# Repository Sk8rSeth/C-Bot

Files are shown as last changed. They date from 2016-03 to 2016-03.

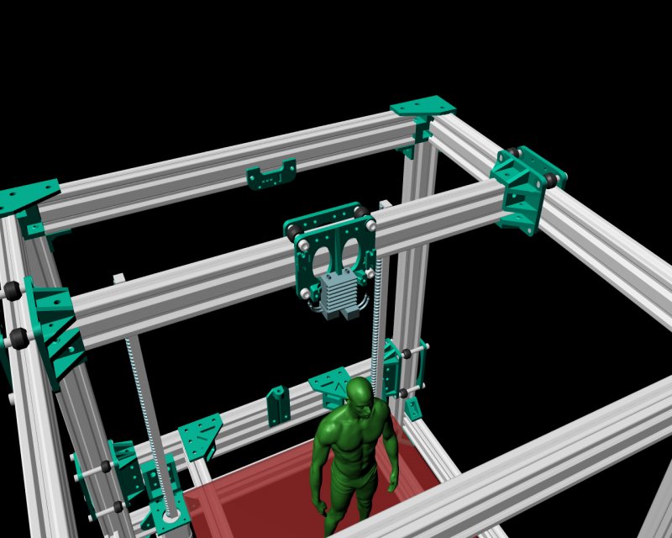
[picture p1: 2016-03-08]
Completed_Builds/Carl_Feniak_Original_C-Bot/Documentation/Assembly Guide/coreXY_detail.jpg

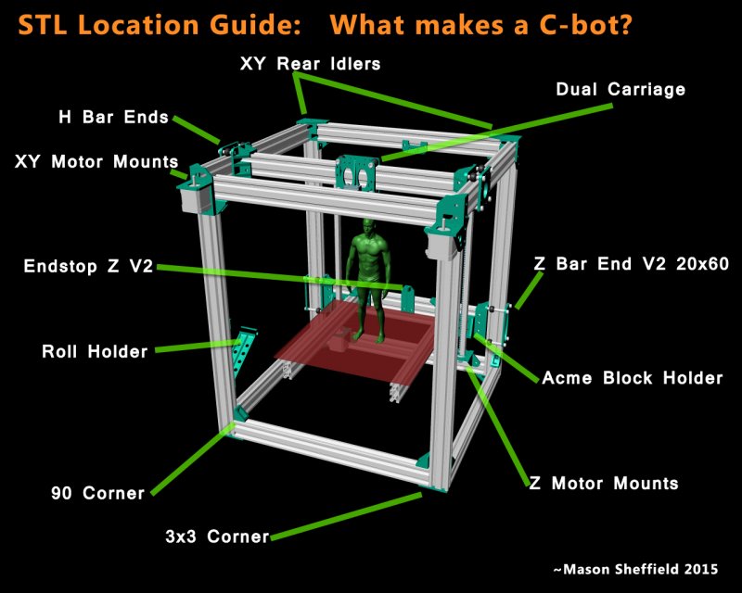
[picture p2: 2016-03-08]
Completed_Builds/Carl_Feniak_Original_C-Bot/Documentation/Assembly Guide/cbot_stlGuide.jpg

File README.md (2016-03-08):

# C-Bot

This repo will serve as the file hosting/iterating source for Carl's C-Bot and its various incarnations.
To contribute to this build, YOUR build must be based on Carl's original c-bot design.
It must be CoreXY mechanics, and most importantly, opensource.

### Anyone is welcome to fork, pull or otherwise grab these files

this will also serve as a place to test experimental builds and parts

# Your Own Build:

file names will be as follows:
	
	- {original_filename}{(#_times_to_print)}.{Author}.{version}
	ex:
		- X_EndStop(x1).CarlFeniak.V2.stl
		- V-Wheel_Spacer(x16).CarlFeniak.v1.stl

### Folder structure MIGHT be as follows, SUBJECT TO CHANGE

{Your Name - Your Build}/

	- Parts/
		- Main_Frame/
		- Z-Bed/
		- XY_Gantry/
		- Other/
		- Test_Parts [each to be deleted when incorporated into final build]/

	- Other_Files [BOM, etc]/

	- Instructions [if any]/

	README.md

the readme.md is the place to show all sorts of info on your build, link to your build log somewhere or thingiverse. its what is displayed when looking at your folder on github.
just like this file is displayed. it might also be a good idea to include YOUR folder structure if its different than the standard, and/or any other notes or progress reports or whatever needs to be seen when looking at your build.

### if you want to add your build to the list, simply submit a pull request with the proper folder structure

Master branch will always be 'stable'. so new people can pull down the master branch at any time and have stable finished builds, that are orginized and easy to navigate. 

### Please create your build in a new branch, named the same as your build to keep pull requests easy

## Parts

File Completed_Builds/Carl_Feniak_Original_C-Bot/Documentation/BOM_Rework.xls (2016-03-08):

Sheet: C-Bot BOM
Price Information Accurate Feb. 2016
BOM
Hardware | AMOUNT | Default | COUNT | USD | Alternatives | COUNT | USD | COMMENT
20x40 Extrusion, 1m | 9 | OpenBuilds, Silver (http://openbuildspartstore.com/v-slot-linear-rail/) | 9 | $18.14 | OpenBuilds, Black (http://openbuildspartstore.com/v-slot-linear-rail/) | 9 | $19.96 | Exact amount depends on the heated bed dimension you get
V-Slot Mini V Wheel | 4x5 | OpenBuilds, Derlin (http://openbuildspartstore.com/delrin-mini-v-wheel/) | 20 | $1.25 | OpenBuilds, Extreme (http://openbuildspartstore.com/xtreme-mini-v-wheel/) | 20 | $3.58
V-Wheel Bearings | 40 | Ebay, MR105ZZ (http://www.ebay.com/itm/10pcs-MR105-MR105ZZ-Miniature-Bearings-Ball-Mini-Bearing-5-X-10-X-4mm-/390391020251) | 4 | $3.28 | Ebay, MR105-2RS (http://www.ebay.ca/itm/10pcs-MR105-2RS-Rubber-Sealed-Ball-Bearing-Miniature-Bearing-5-x-10-x-4mm-Blue-/331662658625) | 4 | $4.00 | you can get the rubber seals in cool colors
Precision shim | 20 | OpenBuilds (http://openbuildspartstore.com/mini-v-wheel-precision-shim/) | 20 | $0.28 |  |  |  | Needed between each pair of V-wheel bearings
Short Spacers | 32 | 3D Print (http://www.openbuilds.com/builds/c-bot.1146/) | 0 | $0.00 | Spacer, 6mm (http://openbuildspartstore.com/aluminum-spacers/) | 40 | $0.28
Long Spacers | 8 | 3D Print (http://www.openbuilds.com/builds/c-bot.1146/) | 0 | $0.00 | Spacer, 20mm (http://openbuildspartstore.com/aluminum-spacers/) | 8 | $0.63
 |  |  |  |  | Extra shims to use above two (http://openbuildspartstore.com/mini-v-wheel-precision-shim/) | 40 | $0.28
8mm lead Screw | 30-50cm x2 | Ebay, combo (http://www.ebay.ca/itm/500mm-Length-Lead-Screw-8mm-Screw-Pitch-Brass-Nut-for-Reprap-3D-Printer-Z-Axis-/261941269628) | 2 | $12.00 | MTW, two start (http://store.makerstoolworks.com/motion/two-start-lead-screw-and-nut-single/) | 2 | $24.95 | 4 Start is typical, but 2 start would be better if you can source it in the length needed
5mm/8mm Flex Coupling | 2 | Ebay, Spiral Type (http://www.ebay.ca/itm/5x8-mm-Motor-Jaw-Shaft-Coupler-5mm-To-8mm-Flexible-Coupling-OD-19x25mm-SU-/221594917783) | 2 | $1.10 | Ebay, Jaw Clamp Type (http://www.ebay.ca/itm/400525695992?_trksid=p2060353.m1438.l2649&ssPageName=STRK%3AMEBIDX%3AIT) | 2 | $8.59 | 3D print (http://www.thingiverse.com/thing:366040)
GT2 16 Tooth Pulley | 2 | Ebay (http://www.ebay.ca/itm/2pcs-GT2-Aluminum-Timing-Pulleys-RepRap-Prusa-Mendel-3D-Printer-16-Tooth-Teeth-/141522888429) | 1 | $5.99 | Amazon, combo (http://www.amazon.com/Anycubic-Timing-Pulleys-Meters-Printer/dp/B0152ZNDLK) | 1 | $14.98
GT2 Belt | 2-5m | Ebay (http://www.ebay.ca/itm/5-Meter-197-6mm-Width-GT2-Timing-Belt-For-3D-printer-Rostock-Mendel-REPRAP-/252232179286) | 1 | $6.20
MK8 drive pulley | 1-2 | Ebay (http://www.ebay.ca/itm/Feedstock-Wheel-Extruder-Gear-Hobbed-Gear-Drive-Gear-for-Reprap-3D-printer-good-/121349742050) | 1 | $2.00 | Ebay, alternate (http://www.ebay.com/itm/1-75-3mm-3D-Printer-MK8-Drive-Gear-for-RepRap-Makerbot-Filament-Extruder-Pulley-/252055736275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)
F623ZZ Flange Bearing | 16 | Ebay (http://www.ebay.com/itm/10-x-F623zz-Mini-Metal-Double-Shielded-Flanged-Ball-Bearings-/231540202636) | 2 | $4.99 | Ebay, alternate (http://www.ebay.ca/itm/10pcs-Mini-F623ZZ-3x10x4mm-Double-Shielded-Flange-Ball-Bearing-Flanged-Bearing-/252169403902) | 2 | $5.60
625ZZ Bearing (for extruder) | 1-2 | Ebay (http://www.ebay.ca/itm/2pcs-625ZZ-Miniature-Bearings-ball-Mini-Bearing-5mm-16mm-5mm-/141204979309) | 1 | $1.99 | Ebay, alternate (http://www.ebay.ca/itm/2pcs-625ZZ-Miniature-Bearings-ball-Mini-Bearing-5mm-16mm-5mm-/141204979309) | 1 | $1.98
1/8" Push In Fitting | 2-4 | Ebay (http://www.ebay.ca/itm/5pcs-1-8-Push-In-Fittings-F-bowden-extruder-1-75mm-4mm-OD-PTFE-Tube-3D-Printer-/331723162262) | 1 | $4.00
Bulldog clips | 8 | Ebay (http://www.ebay.ca/itm/10x-Mini-19mm-Metal-Fold-Back-Letter-Notes-Receipt-Money-File-Paper-Binder-Clips-/351587197720) | 1 | $1.50 | Amazon (http://www.amazon.com/Officemate-Silver-Binder-Assorted-31021/dp/B00006IBA2?s=office-products) | 1 | $2.89
Bed Leveling Springs | 4 | Ebay (http://www.ebay.ca/itm/NEW-4pcs-Heated-Bed-Spring-8mm-3D-Printer-DIY-Accessories-/331324945571) | 1 | $4.00 | homedepot (http://www.homedepot.com/p/Everbilt-Spring-Assortment-Kit-84-Pack-15642/202045461) | 1 | $4.37
Extuder Spring | 1-2 | Hobby Shop? | 1 | $1.00 | Ebay, 7mm OD 25mm L (http://www.ebay.ca/itm/0-6mm-Wire-Diameter-5-50mm-L-304-Stainless-Steel-Pressure-Compression-Spring-/281912361412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) | 1 | 9.99 | Mine was from a random spring kit
Heated Bed, various sizes | 1 | Maker Farm (http://www.makerfarm.com/index.php/heat-beds/12-x-12-heat-bed.html) | 1 | $46.50 | Ebay (http://www.ebay.com/itm/RepRap-PCB-Heatbed-200x300mm-Dual-power-12-24V-Perfect-for-Prusa-i3-etc-/281311483823) | 1 | $19.20
Heated Bed Insulation | 1 | Cardboard | 1 | $0.00 | Amazon (http://www.amazon.com/gp/product/B0018DHBAK?psc=1&redirect=true&ref_=oh_aui_detailpage_o01_s00) | 1 | $10.40
Glass to match heated bed | 1 | Household Store/IKEA | 1 | $10.00 | Voxel Factory (https://www.voxelfactory.com/collections/hardware/products/custom-cut-borosilicate-glass) | 1 | $42.37 | Picture frame sales are a good source of cheap glass, boresilicate is best though
Cable/Zip Tie, 4+ | 4-8 | Ebay (http://www.ebay.ca/itm/New-100pcs-Black-8-3x200mm-Locking-Nylon-Plastic-Cable-Wire-Zip-Ties-Cord-Wrap-/291198607167) | 1 | $2.68 |  |  |  | to hold tube and wires to XY carriage
Electrical
Nema 17 Motor | 5-6 | ATinc, Nema 17 (http://www.automationtechnologiesinc.com/products-page/3d-printer/nema17-stepper-motor-kl17h247-150-4a-for-3d-printer) | 5 | $8.99 | Ebay (http://www.ebay.ca/itm/1pcs-3D-Printers-Reprap-68g-cm2-Lead-1-8-Degree-12V-1-2A-Nema17-Stepper-Motor-/291595158449) | 5 | $18.33 | get 68oz*in or better
12V/30A Power Supply | 1 | Amazon (http://www.amazon.com/gp/product/B00D7CWSCG?psc=1&redirect=true&ref_=oh_aui_detailpage_o03_s00) | 1 | $23.97 | Ebay (http://www.ebay.ca/itm/Hot-12V-30A-AC-DC-PSU-Regulated-Switching-Power-Supply-350W-Brand-New-/262242869774) | 1 | $33.95 | Or repurpose an old PC power supply
Print Control Board | 1 | Ramps 1.4 Kit, Ebay (http://www.ebay.ca/itm/3D-Printer-Kit-RAMPS-1-4-Mega2560-A4988-12864-LCD-Controller-for-Arduino-Reprap-/252181241032) | 1 | $31.99 | Azteeg X3 (http://www.panucatt.com/Azteeg_X3_reprap_3d_printer_controller_p/ax33dp.htm) | 1 | $109.99 | Ramps comes bundled in many types of packages
Stepper Drivers | 5 | DRV8825, Ebay (http://www.ebay.ca/itm/Geeetech-Stepper-driver-Pololu-DRV8825-StepStick-for-RAMPS-Sanguinololu-Teensylu-/331167037633) | 5 | $1.59 |  |  |  | DRV8825 can handle more amps and higher temps than A4998s
Endstop for Y and Z | 2 | Ebay (http://www.ebay.com/itm/3x-Mechanical-End-Stop-Endstop-Switch-Module-V1-2-3D-printer-Reprap-Mendel-Pursa-/271443703227) | 1 | $4.49
Endstop connectors | 2 | Ebay (http://www.ebay.com/itm/20PCS-4-pins-white-Connector-leads-Head-XH2-54-2-54mm-connector-kit-DIP-4p-/330928070002) | 2 | $1.62
Endstop for XY carraige | 1 | Ebay (http://www.ebay.ca/itm/Toggle-Collision-Limit-switch-Travel-Switch-for-Robot-Arduino-Brand-New/351214665011) | 1 | $1.77
HotEnd | 1-2 | Filastuder, E3D Lite (http://www.filastruder.com/products/lite6) | 1 | $39.99 | Filastuder, E3Dv6 (http://www.filastruder.com/products/all-metal-e3d-v6-hotend) | 1 | $79.99
Heated Bed Thermister | 1 | Ebay (http://www.ebay.com/itm/100Kohm-NTC-thermistor-temperture-sensor-for-Reprap-hotbed-PCB-MK2a-heated-bed-/231204000452) | 1 | $0.99
Power Switch/ receptacle | 1 | Ebay (http://www.ebay.ca/itm/Panel-IEC320-C14-Inlet-Power-Socket-On-Off-SPST-Red-Rocker-Switch-AC-250V-10A-/321513901251) | 1 | $3.94 | Amazon (http://www.amazon.com/gp/product/B00511QVVK?psc=1&redirect=true&ref_=od_aui_detailpages00) | 1 | $4.44
Relay | 1 | Ebay, Mech (http://www.ebay.ca/itm/30A-High-Current-Contactor-Switch-12V-Electric-Relay-Board-DC-Power-Control-new-/221977262205) | 1 | $4.26 | Amazon, SSR (http://www.amazon.com/Single-Phase-SSR-40DD-DC3-32V-DC5-60V/dp/B012SW6TB6?s=hi) | 1 | $11.71
Cooling Fan, 40mm | 1-3 | Amazon (http://www.amazon.com/gp/product/B00E1JO8SG?psc=1&redirect=true&ref_=oh_aui_detailpage_o00_s00) | 2 | $2.04 | Ebay (http://www.ebay.ca/itm/1pcs-40mm-x-15mm-12V-2Pin-40-40-15MM-Mini-DC-Cooling-Fan-Brushless-Heatsink-/271700616463) | 2 | $2.99 | look at CFM rating
Wire Wrap | 1m | Ebay (http://www.ebay.ca/itm/10-Feet-3-8-Split-Loom-Wire-Flexible-Tubing-Conduit-Polyethylene-Hose-Sales-/261702819864) | 1 | $3.05
4 Core Project Wire | 10m | Ebay (http://www.ebay.ca/itm/2-6-Multicore-Cable-Flexible-Points-Signal-Small-Power-Data-AUTO-Core-CAR-Wire-/261323374911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) | 1 | $13.99
Dupont Connector Cover, 4 pin | 6 | Ebay (http://www.ebay.ca/itm/100pcs-2-54mm-4P-Pitch-Dupont-Jumper-Wire-Cable-Housing-Female-Pin-Connector-/281215490269) | 1 | $1.59
Dupont Connector Cover, 3 pin | 3 | Ebay (http://www.ebay.ca/itm/100pcs-2-54mm-3P-Pitch-Dupont-Jumper-Wire-Cable-Housing-Female-Pin-Connector-/281215488189) | 1 | $1.29
Dupont Connector Cover, 2 pin | 2-3 | Ebay (http://www.ebay.ca/itm/100pcs-2-54mm-2P-Pitch-Dupont-Jumper-Wire-Cable-Housing-Female-Pin-Connector-/281215486233) | 1 | $1.08
Dupont Female Pins | 37 | Ebay (http://www.ebay.ca/itm/500Pcs-Dupont-Jumper-Wire-Cable-Housing-Female-Pin-Connector-Terminal-2-54mm-L-/252045479834) | 1 | $2.55
Fastners
M3 Socket Bolt, 10mm | 50 | mrmetric (http://www.mrmetric.com/metric-fasteners/metric-socket-screw-steel-alloy-12-9/M10045.html) | 50 | $0.10 |  |  |  | for motor mounts, belt clamps, tube holders, endstop attachment
M3 Socket Bolt, 14mm | 2 | mrmetric (http://www.mrmetric.com/metric-fasteners/metric-socket-screw-steel-alloy-12-9/M10047.html) | 2 | $0.11 |  |  |  | for extruder tension arm pivot
M3 Socket Bolt, 20mm | 17-21 | mrmetric (http://www.mrmetric.com/metric-fasteners/metric-socket-screw-steel-alloy-12-9/M10053.html) | 17 | $0.11 |  |  |  | for leadscrew nut blocks, LCD frame, heated bed
M3 Socket Bolt, 25mm | 12 | mrmetric (http://www.mrmetric.com/metric-fasteners/metric-socket-screw-steel-alloy-12-9/M10054.html) | 12 | $0.18 |  |  |  | for belt idlers and hotend clamps
M3 Nut | 30 | mrmetric (http://www.mrmetric.com/metric-fasteners/sc8z-metric-hex-nut/M50013.html) | 30 | $0.02
M3 Nyloc Nut | 17 | mrmetric (http://www.mrmetric.com/metric-fasteners/sc8z-metric-nylock-nuts/M50303.html) | 17 | $0.02
M3 Washer | 80 | mrmetric (http://www.mrmetric.com/metric-fasteners/metric-flat-washer-steel-zinc/M60010.html) | 80 | $0.01 |  |  |  | for bolts and for spacing flanged bearing to make idlers
M5 Socket Bolt, 10mm | 220 | mrmetric (http://www.mrmetric.com/metric-fasteners/metric-socket-screw-steel-alloy-12-9/M10089.html) | 220 | $0.05 |  |  |  | bracket to extrusion connections (lots!)
M5 Socket Bolt, 12mm | 2 | mrmetric (http://www.mrmetric.com/metric-fasteners/metric-socket-screw-steel-alloy-12-9/M10091.html) | 2 | $0.17 |  |  |  | Y endstop bracket
M5 Socket Bolt, 14mm | 2 | mrmetric (http://www.mrmetric.com/metric-fasteners/metric-socket-screw-steel-alloy-12-9/M10093.html) | 2 | $0.16 |  |  |  | Z endstop bracket
M5 Socket Bolt, 40mm | 13 | mrmetric (http://www.mrmetric.com/metric-fasteners/metric-socket-screw-steel-alloy-12-9/M10106.html) | 13 | $0.18 |  |  |  | XY Slides and XY Carriage + Z axis fine adjustment
M5 Socket Bolt, 60mm | 8 | mrmetric (http://www.mrmetric.com/metric-fasteners/metric-socket-screw-steel-alloy-12-9/M10323.html) | 8 | $0.40 |  |  |  | Z Slides
M5 Nyloc Nut | 20 | mrmetric (http://www.mrmetric.com/Discount-Items/Discount-Metric-Nuts/M50306.html) | 20 | $0.07 |  |  |  | V wheel assemblies
M5 Washer | 250 | mrmetric (http://www.mrmetric.com/metric-fasteners/metric-flat-washer-steel-zinc/M60019.html) | 250 | $0.01 |  |  |  | V wheel assemblies, frame construction
M5 Tee Nuts | 225 | OpenBuilds, T-Nuts (http://openbuildspartstore.com/tee-nuts-25-pack/) | 9 | $6.89 | mrmetric, Square Nuts (http://www.mrmetric.com/metric-fasteners/sc4z-metric-square-nuts/M53065.html) | 225 | $0.04 | Don't cheap out and print nuts (my advice from experience)
 |  |  |  | 624.89 | USD
Optional
Dupont Connector Crimp Pliers | 1 | Ebay (http://www.ebay.ca/itm/Pin-Crimping-Tool-Crimper-2-54mm-3-96mm-KF2510-28-18-AWG-Plier-0-1-1-0m-YUCA-/291275778695) | 1 | 12
M3 Thumb Nuts, for bed leveling | 5 | mrmetric (http://www.mrmetric.com/metric-fasteners/sc8z-metric-knurled-nuts/M50759.html) | 5 | $1.32
M5 Thumb Nut, for extruder idler spring | 2 | mrmetric (http://www.mrmetric.com/metric-fasteners/sc8z-metric-knurled-nuts/M50782.html) | 2 | $1.17
Extra Strength Hair Spray | 1 | Local Drug Store | 1 | $8.00
8mm threaded rod for roll holder | 1 | Local Hardware | 1 | $8.00
+ 8mm nut | 2-4 | mrmetric (http://www.mrmetric.com/metric-fasteners/sc10z-metric-hex-nut-m8/) | 2 | $0.12
+ 608ZZ Bearings | 2-4 | Ebay (http://www.ebay.ca/itm/10-x-608ZZ-Deep-Groove-Ball-Bearings-8-22-7mm-for-3D-Printer-8mm-Bore-/261953133583) | 1 | $3.99
M5 Washer 15mm OD | 2 | mrmetric (http://www.mrmetric.com/metric-fasteners/metric-flat-large-od-washer-steel-z/M60355.html) | 2 | $0.03 |  |  |  | Larger Washer for Extruder Spring
M5 Low Profile Bolt, 10mm | 16 | mrmetric (http://www.mrmetric.com/metric-fasteners/metric-button-socket-screws-steel-10-9/M11410.html) | 16 | $0.10 |  |  |  | Optional: for inside of lower frame corner brackets
LEDS | 1 | Amazon (http://www.amazon.com/gp/product/B006LW2NJM?psc=1&redirect=true&ref_=od_aui_detailpages00) | 1 | $8.69 | Ebay (http://www.ebay.ca/itm/10M-600LEDS-3528-SMD-RGB-2X-5M-LED-light-strip-44-Key-IR-Remote-Controller-LU-/161811338109) | 1 | $9.00
Thermal Paste | 1 | Amazon (http://www.amazon.com/gp/product/B00KAOP4SY?psc=1&redirect=true&ref_=oh_aui_detailpage_o02_s00) | 1 | $4.99
 |  |  |  | 56.51 | USD

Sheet: Extrusions Lengths
Heated Bed Dimensions:
If your bed is not square, put the longer side as the length (L)
 | L | W |  | Conversion table
Enter--> | 320 | 320 | mm |  | L | W
***bed mount hole to mount hole |  |  |  | 10x10 | 269 | 269
 |  |  |  | 8x12 | 320 | 218
 |  |  |  | 12x12 | 320 | 320
Lead Screw Length:
 | L
 | 300 | mm
Cut Aluminum lengths to:
Count | Length |  | Purpose
X4 | 480 | mm | <-- front/back, top/bottom horizontal stationary pieces
X1 | 466 | mm | <-- the back/Z moving piece
X1 | 506 | mm | <-- the top/XY moving piece
X2 | 480 | mm | <-- top sides |  |  |  | increase these by ~30mm
X2 | 460 | mm | <-- bottom sides |  |  |  | increase these by ~30mm
X4 | 450 | mm | <-- legs, gives some flexibility for hotend length and mounting |  |  |  | add 20mm, but double check leadscrew impact of new mounts
X2 | 445 | mm | <-- bed support
x1 | 240 | mm | <-- bed front cross piece
 | 7462 | mm
 | 7.462 | m | <-- there will be wastage, so buy more

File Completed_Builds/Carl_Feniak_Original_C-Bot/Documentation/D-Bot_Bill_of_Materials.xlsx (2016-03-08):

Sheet: Bill of Materials
 | Item | Source | Qty. | Unit Cost | Ext. Cost | Link | Comments | Additional Comments
Frame | V Slot Extrusion | Open Builds Store |  |  |  |  | Frame sized for 200x300mm bed and 320mm print height | OpenBuilds occasionally has free shipping weekends
 | - 20x20x1500mm | Open Builds Store | 2 | $15.00 | $30.00 | V Slot Linear Rail (http://openbuildspartstore.com/v-slot-linear-rail/)
 | - 20x40x1500mm | Open Builds Store | 2 | $19.50 | $39.00 | V Slot Linear Rail (http://openbuildspartstore.com/v-slot-linear-rail/)
 | - 20x40x1000mm | Open Builds Store | 2 | $13.00 | $26.00 | V Slot Linear Rail (http://openbuildspartstore.com/v-slot-linear-rail/)
Electrical | E3D v6 Hot End 1.75 w/ Bowden extras | Filastruder | 1 | $78.89 | $78.89 | 1.75 E3D v6 w/bowden extras (http://www.filastruder.com/products/all-metal-e3d-v6-hotend) | E3Dv6 with bowden tube and coupling (coupon code cheapv6) | For half the cost, E3D v6 lite would work well for PLA and ABS only.
 | Nema 17 Stepper Motor | AutomationDirect | 5 | $11.26 | $56.30 | Stepper Motor (http://www.automationtechnologiesinc.com/products-page/3d-printer/nema17-stepper-motor-kl17h247-150-4a-for-3d-printer)
 | 12V/30A Power Supply | Amazon | 1 | $23.97 | $23.97 | Power Supply (http://www.amazon.com/gp/product/B00D7CWSCG?psc=1&redirect=true&ref_=oh_aui_detailpage_o03_s00)
 | Ramps 1.4 Kit | Ebay | 1 | $32.00 | $32.00 | Ramps 1.4 kit (http://www.ebay.com/itm/171908397844?_trksid=p2060353.m2749.l2649&ssPageName=STRK%3AMEBIDX%3AIT)
 | Heated Bed | Ebay | 1 | $28.86 | $28.86 | PCB Heated Bed (http://www.ebay.com/itm/RepRap-PCB-Heatbed-200x300mm-Dual-power-12-24V-Perfect-for-Prusa-i3-etc-/281311483823) | 200mmx300mm (~8"x~12") 12v | This heated bed works for 60C but it has difficulty maintaining 100C. Consider alternative if printing ABS.
 | Solid State DC Relay | Amazon | 1 | $9.87 | $9.87 | SSR DC DC Relay (http://www.amazon.com/Single-Phase-SSR-40DD-DC3-32V-DC5-60V/dp/B012SW6TB6?s=hi) | Solid State AC relay will not work with a DC load | Don't confuse with the SS AC relay, they look similar, read the label
 | 100k 3950 Thermistor for bed | Ebay | 1 | $1.00 | $1.00 | 3950 Thermistor (http://www.ebay.com/itm/100Kohm-NTC-thermistor-temperture-sensor-for-Reprap-hotbed-PCB-MK2a-heated-bed-/231204000452) | For heated bed temperature feedback | Alternate Thermistor 10pk (http://www.amazon.com/gp/product/B00GD471PO?psc=1&redirect=true&ref_=oh_aui_detailpage_o04_s00)
 | Endstop 3 pack, v1.2 | Ebay | 1 | $4.49 | $4.49 | Endstop Pack (http://www.ebay.com/itm/3x-Mechanical-End-Stop-Endstop-Switch-Module-V1-2-3D-printer-Reprap-Mendel-Pursa-/271443703227) | 3 pack
 | 40mm cooling fans | Amazon | 2 | $2.04 | $4.08 | 40mm fan (http://www.amazon.com/gp/product/B00E1JO8SG?psc=1&redirect=true&ref_=oh_aui_detailpage_o00_s00) | Ducted print fan and Ramps board cooling
 | Alternate fan for E3Dv6 heatsink | Digi-key | 1 |  |  | 30mm Fan (https://www.digikey.com/product-detail/en/MC30101V2-000U-A99/259-1549-ND/2757780) | Optional, Alternate quieter fan for the E3D V6 heatsink
 | 2.54mm Connector kit | Ebay | 1 | $3.00 | $3.00 | 2.54 Connector Pins (http://www.ebay.com/itm/100Pcs-1P-Dupont-Jumper-Cable-Housing-100pcs-Female-Connector-Terminal-2-54mm-/161876957933) | For 1, 2, 3, 4 pin connections to Ramps board headers | Requires a HT-225D type crimping tool, or careful soldering of wire to each pin
 | XH2.54 Connector Kit | Ebay | 1 | $2.00 | $2.00 | XH2.54 4 Pin Connectors (http://www.ebay.com/itm/20PCS-4-pins-white-Connector-leads-Head-XH2-54-2-54mm-connector-kit-DIP-4p-/330928070002) | To plug into the three endstop jacks | Requires a HT-225D type crimping tool, or careful soldering of wire to each pin
 | Wire | Various | 1 | $10.00 | $10.00 |  | 22awg wire for motors, endstops, fans, thermistors. | 14awg wire for heated bed and Ramps supply
 | Receptacle/Switch for 120v power | Amazon | 1 | $4.05 | $4.05 | IEC320 Male Jack with Switch (http://www.amazon.com/gp/product/B00511QVVK?psc=1&redirect=true&ref_=od_aui_detailpages00) | Optional, also needs a 5A fuse | 5A Fuse (http://www.amazon.com/Qty-Fast-Blow-Fuse-250v-GMA5A/dp/B004HLV372?s=industrial)
 | 12v 5050 LED Strip ~45" | Amazon | 1 | $8.00 | $8.00 | 5m 5050 LED Strip (http://www.amazon.com/gp/product/B006LW2NJM?psc=1&redirect=true&ref_=od_aui_detailpages00) | Optional | Optional controller w/ remote, LED strip can also be connected directly to 12v supply (http://www.amazon.com/gp/product/B00JRVSO38?psc=1&redirect=true&ref_=oh_aui_detailpage_o07_s00)
Mechanical | V-Slot Mini V Wheel | Open Builds Store | 20 | $0.90 | $17.95 | Mini V Wheel (http://openbuildspartstore.com/delrin-mini-v-wheel/) | Select the 20pk for a price break
 | MR105ZZ 5mmx10mmx4mm bearings | Ebay | 40 | $0.38 | $15.00 | Wheel Bearings 10pk (http://www.ebay.com/itm/10pcs-MR105-MR105ZZ-Miniature-Bearings-Ball-Mini-Bearing-5-X-10-X-4mm-/390391020251) | Need 40, order 4x 10pk
 | F623ZZ Flange Bearing 3x10x4mm | Ebay | 16 | $0.79 | $12.58 | Flanged Bearing (http://www.ebay.com/itm/10-x-F623zz-Mini-Metal-Double-Shielded-Flanged-Ball-Bearings-/231540202636) | Need 16, order 2x 10pk
 | 625ZZ Bearing | Ebay | 1 | $1.98 | $1.98 | 625ZZ Bearing (http://www.ebay.com/itm/1pc-625ZZ-Miniature-Bearings-ball-Mini-Bearing-5mm-16mm-5mm-Chrome-Steel-/141203832291) | For Extruder
 | 8mm lead Screw, 400 mm | Ebay | 2 | $13.23 | $26.46 | Lead Screw (http://www.ebay.com/itm/400mm-Lead-Screw-Z-Axis-8mm-Screw-Pitch-W-Brass-Nut-For-3D-Printer-Accessory-/321772264121) | Comes with nut
 | 5mm x 8mm Flex Coupling | Ebay | 2 | $2.50 | $5.00 | Flex Coupling (http://www.ebay.com/itm/2-PCS-Flexible-Coupler-5-x-8-mm-for-3D-Printer-Z-Axis-RepRap-Mendel-Prusa-CNC-/121631998558) | Order 2pk
 | Kit, 2 GT2 Pulley and 2m GT2 belt | Ebay | 1 | $11.99 | $11.99 | Pulleys and Belt (http://www.ebay.com/itm/2-x-Aluminum-GT2-16T-Pulley-and-2M-Belt-for-RepRap-3D-printer-Prusa-i3-Mendel-/221893428403) | Comes with (2) GT2 16t Pulley and (1) 2m GT2 Belt
 | GT2 Belt, 2m | Ebay | 1 | $8.00 | $8.00 | GT2 Belt (http://www.ebay.com/itm/GT2-Timing-Belt-for-3D-printer-cut-to-length-reprap-prusa-mendel-/321688968867) | GT2 belt cut to length, 2m (~7ft) | Total of 2x2m belts needed
 | 1.75mm MK8 drive pulley | Ebay | 1 | $2.29 | $2.29 | 1.75mm MK8 Pulley (http://www.ebay.com/itm/1-75-3mm-3D-Printer-MK8-Drive-Gear-for-RepRap-Makerbot-Filament-Extruder-Pulley-/252055736275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)
Misc. | Spring Kit | Home Depot | 1 | $2.00 | $2.00 | Spring Kit (http://www.homedepot.com/p/Everbilt-Spring-Assortment-Kit-84-Pack-15642/202045461) | Four bed leveling springs and one extruder tensioner spring
 | Glass to match heated bed | Hardware Store | 1 | $6.00 | $6.00 |  | 1/8" Thick, 12 3/8" x 8 7/16" | This dimension for the glass assumes that the corners will be notched around the bolt heads.
 | Binder clips | Desk Drawer | 8 | $0.10 | $0.80 | Binder Clips (http://www.amazon.com/Officemate-Silver-Binder-Assorted-31021/dp/B00006IBA2?s=office-products) | Raid your local office supply cabinet or desk drawer
 | Thermal adhesive | Amazon | 1 | $2.00 | $2.00 | For heatsinks, thermistors (http://www.amazon.com/gp/product/B00KAOP4SY?psc=1&redirect=true&ref_=oh_aui_detailpage_o02_s00)
 | Rubber Feet | Amazon | 4 | $0.50 | $2.00 | Rubber Feet (http://www.amazon.com/gp/product/B008LTY1NO?psc=1&redirect=true&ref_=od_aui_detailpages00) | Need 4, ordered 5pk
 | Insulation for bottom of bed | Amazon | 1 | $2.00 | $2.00 | Corkboard (http://www.amazon.com/gp/product/B0018DHBAK?psc=1&redirect=true&ref_=oh_aui_detailpage_o01_s00) | Optional, Attach corkboard to bottom of heatbed with JBweld
 | Wire Spiral Wrap, 3m | Amazon | 1 | $3.00 | $3.00 | Wiring Tube (http://www.amazon.com/gp/product/B00U8LA25O?psc=1&redirect=true&ref_=oh_aui_detailpage_o03_s00) | Optional, For wire management
 | PLA Spool, 1kg | Amazon | 1 | $22.98 | $22.98 | Hatchbox 1.75mm Green (http://www.amazon.com/HATCHBOX-1-75mm-3D-Printer-Filament/dp/B00J0GQ2OS?s=industrial) | At least one spool is needed to print all parts
Print | 1mm Shim, 5mm ID 8mm OD | Print | 20 |  |  | D-Bot Thing Files (http://www.thingiverse.com/thing:1001065/) | One in the center of each wheel, between the bearings
 | 7mm Spacer, 5mm ID 8mm OD | Print | 32 |  |  | D-Bot Thing Files (http://www.thingiverse.com/thing:1001065/) | Two for each wheel. Z axis only needs one per wheel.
 | 90 deg Corner | Print | 14 |  |  | D-Bot Thing Files (http://www.thingiverse.com/thing:1001065/)
 | 3x3 Corner | Print | 10 |  |  | D-Bot Thing Files (http://www.thingiverse.com/thing:1001065/)
Hardware | M3 Socket Bolt, 8mm | MrMetric | 31 | $0.10 | $3.10 | M3 x 8mm Bolt (http://www.mrmetric.com/metric-fasteners/metric-socket-screw-steel-alloy-12-9/M10043.html)
 | M3 Socket Bolt, 10mm | MrMetric | 9 | $0.05 | $0.45 | M3 x 10mm Bolt
 | M3 Socket Bolt, 20mm | MrMetric | 13 | $0.11 | $1.43 | M3 x 20mm Bolt (http://www.mrmetric.com/metric-fasteners/metric-socket-screw-steel-alloy-12-9/M10053.html)
 | M3 Socket Bolt, 25mm | MrMetric | 15 | $0.18 | $2.70 | M3 x 25mm Bolt (http://www.mrmetric.com/metric-fasteners/metric-socket-screw-steel-alloy-12-9/M10054.html)
 | M3 Nut | MrMetric | 30 | $0.02 | $0.60 | M3 Nut (http://www.mrmetric.com/metric-fasteners/sc8z-metric-hex-nut/M50013.html)
 | M3 Nyloc Nut | MrMetric | 17 | $0.02 | $0.34 | M3 Nylock Nut (http://www.mrmetric.com/metric-fasteners/sc8z-metric-nylock-nuts/M50303.html)
 | M3 Washer | MrMetric | 80 | $0.01 | $0.80 | M3 Washer (http://www.mrmetric.com/metric-fasteners/metric-flat-washer-steel-zinc/M60010.html)
 | M4 Bolt, 30mm | MrMetric | 4 | $0.14 | $0.56 | M4 x 30mm Bolt (http://www.mrmetric.com/metric-fasteners/metric-socket-screws-steel-8-8-z/M10876.html)
 | M4 washer | MrMetric | 4 | $0.01 | $0.04 | M4 Washer (http://www.mrmetric.com/metric-fasteners/metric-flat-washer-steel-zinc/M60015.html)
 | M5 Socket Bolt, 10mm | MrMetric | 198 | $0.05 | $9.90 | M5 x 10mm Bolt (http://www.mrmetric.com/metric-fasteners/metric-socket-screw-steel-alloy-12-9/M10089.html)
 | M5 Socket Bolt, 12mm | MrMetric | 1 | $0.17 | $0.17 | M5 x 12mm Bolt (http://www.mrmetric.com/metric-fasteners/metric-socket-screw-steel-alloy-12-9/M10091.html)
 | M5 Socket Bolt, 20mm | MrMetric | 1 | $0.14 | $0.14 | M5 x 20mm Bolt (http://www.mrmetric.com/metric-fasteners/metric-socket-screw-steel-alloy-12-9/M10098.html)
 | M5 Socket Bolt, 40mm | MrMetric | 22 | $0.18 | $3.96 | M5 x 40mm Bolt
 | M5 Socket Bolt, 75mm | MrMetric | 1 | $0.05 | $0.05 | M5 x 75mm Bolt (http://www.mrmetric.com/Discount-Items/discounted-metric-socket-head-cap-screws/M11104.html)
 | M5 Nut | MrMetric | 9 | $0.03 | $0.27 | M5 Nut (http://www.mrmetric.com/metric-fasteners/sc8z-metric-hex-nut/M050020Y.html)
 | M5 Nyloc Nut | MrMetric | 14 | $0.07 | $0.98 | M5 Nylock Nut (http://www.mrmetric.com/Discount-Items/Discount-Metric-Nuts/M50306.html)
 | M5 Square Nut | MrMetric | 187 | $0.01 | $1.87 | M5 Square Nut (http://www.mrmetric.com/metric-fasteners/sc4z-metric-square-nuts/M53065.html) | The equivalent amount of OpenBuilds T-nuts is $40. | Square nuts are used instead because they are much cheaper and function nearly the same.
 | M5 Washer | MrMetric | 224 | $0.01 | $2.24 | M5 Washer (http://www.mrmetric.com/metric-fasteners/metric-flat-washer-steel-zinc/M60019.html)
 | M5 Washer 15mm OD | MrMetric | 2 | $0.03 | $0.06 | M5 Washer 15mm OD (http://www.mrmetric.com/metric-fasteners/metric-flat-large-od-washer-steel-z/M60355.html)
 | M5 Phillips Flathead Bolt, 8mm | MrMetric | 2 | $0.16 | $0.32 | M5 x 8mm Phillips Flathead (http://www.mrmetric.com/metric-fasteners/Steel-Grade-4-8-Zinc-Metric-Flat-Head-Screw/M30838B.html) | Optional, for printed cable chain ends
 | See sheet two for hardware detail |  | These are all minimum quantities, order extra if needed.
 |  |  |  |  | $95.00 | Frame Total
 |  |  |  |  | $266.51 | Electrical Parts Total
 |  |  |  |  | $101.25 | Mechanical Parts Total
 |  |  |  |  | $40.78 | Miscellaneous Parts Total
 |  |  |  |  | $29.98 | Hardware Total
 |  |  |  |  | $533.52 | Grand Total

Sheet: Hardware Quantities
 | Qty | Type | Diameter | Length | Application Notes
Frame (PLA to Vslot) | 198 | Bolt | M5 | 10mm | See subtotal box -------------------------------------------------> | Frame (PLA bolted to Vslot)
 | 184 | Square Nut | M5 |  | Less 14 for M5 tapped mounts | 50 | 3x3 Corner plates (5 Ea.)
 | 198 | Washer | M5 |  |  | 28 | 90˚ brackets (2 Ea.)
Wheel Axles | 20 | Bolt | M5 | 40mm |  | 24 | Rear XY Idlers (12 ea.)
 | 12 | Nyloc Nut | M5 |  | Moving XY idlers and print carrraige | 20 | XY Motor Mounts (10 Ea.)
 | 8 | Nut | M5 |  | Z wheels | 12 | Z guides (3 Ea.)
 | 24 | Washer | M5 |  | 2 per axle, none on Z axles | 12 | Heated Bed Brackets (3 Ea.)
Extruder | 1 | Bolt | M5 | 40mm | Tensioner Flange | 12 | Miscellaneous/ Future
 | 1 | Bolt | M5 | 12mm | 625zz Bearing Mount | 8 | Lead Screw Brackets (4 Ea.)
 | 1 | Nut | M5 |  | Tensioner Flange | 8 | Moving XY idlers (4 Ea.)
 | 1 | Nylock Nut | M5 |  | 625zz Bearing Mount | 8 | Z motor mounts ( 4 ea.)
 | 2 | Washer | M5 |  | Tensioner Flange | 6 | End stop mounting (2 Ea.)
Cable Chain | 2 | Bolt, Phillips Flat | M5 | 8mm | Cable chain ends | 6 | 2x1 Corner Plates (3 ea.)
 | 2 | Square Nut | M5 |  |  | 2 | Power Switch Mount
Spool Holder | 1 | Bolt | M5 | 75mm | Sized for Hatchbox 1kg spool | 2 | Extruder
 | 1 | Square Nut | M5 |  |  | 198 | Subtotal
 | 1 | Nylock Nut | M5
 | 2 | Washer 15mm OD | M5
Endstops | 1 | Bolt | M5 | 40mm | Z actuator
 | 1 | Bolt | M5 | 20mm | Y actuator | Minimum Quantities Required
 | 1 | Bolt | M3 | 25mm | X actuator | Qty | Type | Diameter | Length
 | 6 | Bolt | M3 | 8mm | Endstop Switch Mounting | 31 | Bolt | M3 | 8mm
 | 6 | Nut | M3 |  |  | 9 | Bolt | M3 | 10mm
 | 6 | Washer | M3 |  |  | 13 | Bolt | M3 | 20mm
Idler Pulleys | 8 | Bolt | M3 | 25mm |  | 15 | Bolt | M3 | 25mm
 | 4 | Nyloc Nut | M3 |  | Moving XY idlers | 30 | Nut | M3
 | 4 | Nut | M3 |  | Rear XY idlers | 17 | Nyloc Nut | M3
 | 16 | Washer | M3 |  | For moving XY idlers/ in between flanged bearings | 80 | Washer | M3
Print Carriage | 4 | Bolt | M3 | 8mm | Hot end clamp top, Tube holder
 | 8 | Bolt | M3 | 10mm | Belt Clamps | 4 | Bolt | M4 | 30mm
 | 2 | Bolt | M3 | 25mm | Hot End Clamp bottom | 4 | Washer | M4
 | 14 | Nut | M3
 | 14 | Washer | M3 |  |  | 2 | Bolt, Phillips Flat | M5 | 8mm
Print bed | 4 | Bolt | M3 | 25mm | Bed leveling | 198 | Bolt | M5 | 10mm
 | 8 | Bolt | M3 | 20mm | Lead Screw Nut Mounts | 1 | Bolt | M5 | 12mm
 | 4 | Nut | M3 |  | Bed leveling | 1 | Bolt | M5 | 20mm
 | 8 | Nyloc Nut | M3 |  | Lead Screw Nut Mount | 22 | Bolt | M5 | 40mm
 | 16 | Washer | M3 |  | Bed leveling, lead screw mounts | 1 | Bolt | M5 | 75mm
Motor Mounts | 19 | Bolt | M3 | 8mm |  | 9 | Nut | M5
 | 1 | Bolt | M3 | 10mm | Extruder tensioner flange hole | 14 | Nyloc Nut | M5
 | 20 | Washer | M3 |  |  | 187 | Square Nut | M5
Print Fan | 5 | Bolt | M3 | 20mm | Fan Mounting, Fan Swivel | 224 | Washer | M5
 | 2 | Bolt | M3 | 8mm | Mount to print carriage | 2 | Washer 15mm OD | M5
 | 2 | Nut | M3 |  | Mount to print carriage
 | 5 | Nylock Nut | M3 |  | Fan Mounting, Fan Swivel | These are all minimum quantities, order extra hardware if you like to have spares
 | 8 | Washer | M3
Power Supply | 4 | Bolt | M4 | 30mm | Power Supply Clamps
 | 4 | Washer | M4

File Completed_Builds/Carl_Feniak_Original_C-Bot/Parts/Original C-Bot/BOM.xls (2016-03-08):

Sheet: C-Bot BOM
BOM
ITEM | AMOUNT | SOURCE1 | COUNT | USD | SOURCE2 | COUNT | USD | COMMENT
V-Slot Mini V Wheels | 4x5 | Open Builds Store | 20 | $3.99 |  |  |  | updated 11/06/2015 for cahnge to "kit" contents
1mm shim, 5mm ID | 0 | Open Builds Store | 0 | $0.25 | if necessary--> | 40 |  | if you get the proper spec spacers then extras of these aren't necessary
Aluminum Spacers, 1/4" | 32 | Open Builds Store | 12 | $0.25
20x40 Extrusion, 1m | 8 | Open Builds Store | 8 | $14.52 |  |  |  | Exact amount depends on the heated bed dimension you get
8mm lead Screw, 30 cm | 30cm X 2 | Open Builds Store | 2 | $11.21
8mm Acme Nut Block | 2 | Open Builds Store | 2 | $7.79
M5 Tee Nuts, 25 pk | 129 | Open Builds Store | 7 | $5.55 |  |  |  | Don't cheap out and print nuts
5mm/8mm Flex Coupling | 2 | Open Builds Store | 2 | $7.12 | Ebay or 3D print | 2 | 4.49 | http://www.thingiverse.com/thing:366040
90 deg Corner | 10 | Open Builds Store | 10 | $3.08 | 3D print |  |  | http://www.thingiverse.com/thing:287293
5 hole 90 Deg Plate | 8 | Open Builds Store | 8 | $5.38 | 3D print |  |  | http://www.thingiverse.com/thing:287293
Nema 17 Motor | 5 | Open Builds Store | 5 | $19.61 | Ebay | 1 | 99.99 | get 68oz*in or better
12V/30A Power Supply | 1 | Open Builds Store | 1 | $39.23 | Ebay | 1 | 29.79
Ramps 1.4 Kit | 1 | Ebay | 1 | $36.95
GT2 16 Tooth Pulley | 2 | Ebay | 1 | $4.49
GT2 Belt | 2m | Ebay | 2 | $3.78
mk8 drive pulley | 1 | Ebay | 1 | $5.00
Endstop, mech v1.2, 3 pk |  | Ebay | 1 | $9.95
F623ZZ Flange Bearing 3x10x4mm, 10 pk |  | Ebay | 2 | $7.99
625ZZ Bearing, 1 |  | Ebay | 1 | $2.50
PTFE Bowden Tube, 2x4mm, 1m |  | Ebay | 1 | $4.50
Push Fit Coupling 4mm ID 5mm OD, 2 |  | Ebay | 1 | $4.00
Wire Spiral Wrap, 1m |  | Ebay | 1 | $1.00
Bulldog clips, 6 |  | Ebay | 1 | $1.50
Bed Leveling Springs, 4pk |  | Ebay | 1 | $4.00
Heated Bed, various sizes | 1 | Maker Farm | 1 | $35.00 | Ebay | 1 | 20 | Ebay is good for an MK2 (8x8)
Glass to match heated bed | 1 | Voxel Factory/ Ebay | 1 | $40.00 | Household Store | 5 |  | Picture frame sales are a good source of cheap glass
J-Head, 1.75 Filament, 0.4mm Nozzle | 1 | Various | 1 | $55.00 |  |  |  | Get an official J-Head, worth the extra $$$
M3 nuts | 34 | Element 14 | 1 | $2.41
M3 Washers | 70 | Element 14 | 1 | $2.41
M3 socket bolt, 10mm | 42 | Element 14 | 1 | $10.21
M3 socket bolt, 25mm | 14 | Element 14 | 1 | $12.55
M5 nyloc nuts | 1 | Element 14 | 1 | $3.33
M5 Washers | 1 | Element 14 | 1 | $2.21
M5 socket bolt, 40mm | 22 | Element 14 | 1 | $10.23
M5 socket bolt, 16mm | 3 | Element 14 | 1 | $5.71
M5 socket bolt, 10mm | 141 | Element 14 | 2 | $8.69
 |  |  |  | $795.04 | USD | <-- you can do better than this with ebay kits and auctions
Optional
60mm M5 bolts for V2 Z axis | 8 | Ebay | 1 | 10
DRV8825 Drivers | 5 | Ebay | 1 | 23.5
LCD, Full Graphic w adapter | 1 | Ebay | 1 | 17.27 | LCD, 2004 (smaller) | 1 | 12.19
+ 46cm or more 10 pin flat ribbon cable | 2 | Ebay | 1 | 5 |  |  |  | May be needed depending on positioning
Rubber Feet, 17x10mm | 4 | Ebay | 1 | 3.97
DC Relay, heated beds over 8"x8" | 1 | Maker Farm | 1 | 15 | Ebay | 5.83
Cooilng Fans, 40x40mm | 3 | Ebay | 3 | 3.29 |  |  |  | look at CFM rating
Ramps Fan Expansion, Ebay | 1 | Ebay | 1 | 7.5
Wiring Kit, Ebay | 1 | Ebay | 1 | 6.5 |  |  |  | Ramps board use "Dupont 2.54mm" connectors
Cable/Zip Tie, 4+ | 4 | Local Hardware | 1 | 1
Extuder Spring | 1 | Hobby Shop? | 1 | 1 |  |  |  | Mine was from a random spring kit
M3 Thumb Nuts, for bed leveling | 5 | Element 14 | 5 | 1.18 |  |  |  | Fancy, but there are printable option you can make after
M5 Thumb Nut, for extruder idler spring | 2 | Element 14 | 2 | 1.84
Power Switch for AC Plug | 1 | Ebay
Extra Strength Hair Spray | 1 | Local Drug Store | 1 | 8 |  |  |  | I print PLA and ABS on a hair sprayed heated bed
8mm threaded rod for roll holder | 1 | Local Hardware | 1 | 8
+ 8mm nut | 1 | Local Hardware | 1 | 0.12
+ 625ZZ Bearings | 2 | Ebay | 2 | 0.99
 |  |  |  | 128.29 | USD

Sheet: Extrusions Lengths
Heated Bed Dimensions:
If your bed is not square, put the longer side as the length (L)
 | L | W |  | Conversion table
Enter--> | 305 | 203 | mm |  | L | W
 |  |  |  | 8x8 | 203 | 203
 |  |  |  | 10x10 | 254 | 254
 |  |  |  | 8x12 | 305 | 203
 |  |  |  | 12x12 | 305 | 305
Lead Screw Length: |  |  |  | Note: for beds widths over 8", you might want to upgrade the Z axis moving piece to 20x60 extrusion. (leave the other at 20x40)
 | L
 | 300 | mm
Cut Aluminum lengths to:
X4 | 483 | mm | <-- front/back, top/bottom stationary pieces
X1 | 469 | mm | <-- the back/Z moving piece, *** see note above
X1 | 509 | mm | <-- the top/XY moving piece
X2 | 333 | mm | <-- top sides
X2 | 313 | mm | <-- bottom sides
X4 | 410 | mm | <-- legs, gives some flexibility for hotend length and mounting
X2 | 303 | mm | <-- bed support
 | 6448 | mm
 | 6.448 | m | <-- there will be wastage, so buy more

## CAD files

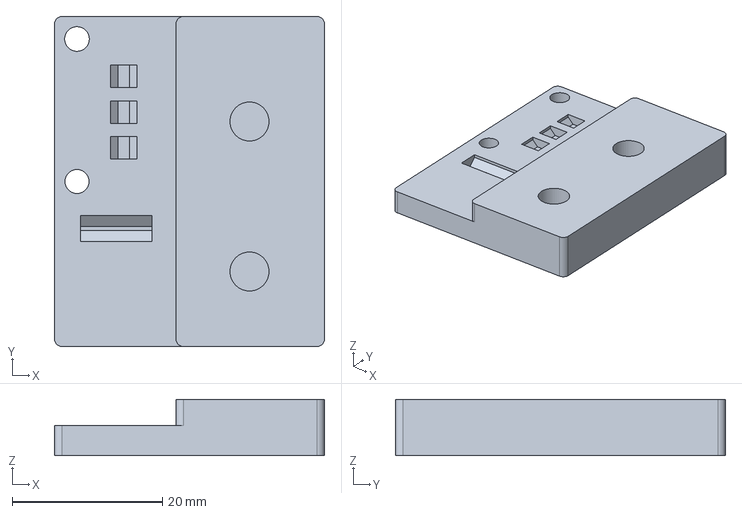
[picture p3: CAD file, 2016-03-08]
Completed_Builds/Carl_Feniak_Original_C-Bot/Parts/Original C-Bot/C-bot - STEP files_Rev2/C-Bot EndStop X.stp
36.0 x 44.0 x 7.50 mm

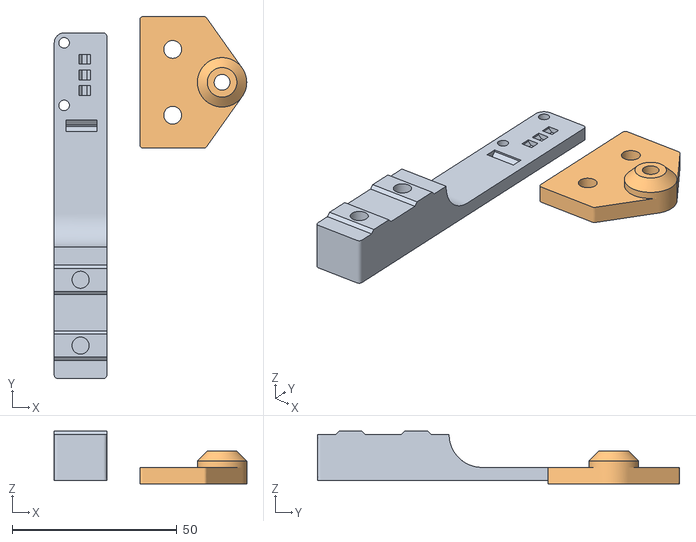
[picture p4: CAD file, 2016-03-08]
Completed_Builds/Carl_Feniak_Original_C-Bot/Parts/Original C-Bot/C-Bot STL Files/Endstop Z V2.stl
58.5 x 110.0 x 16.0

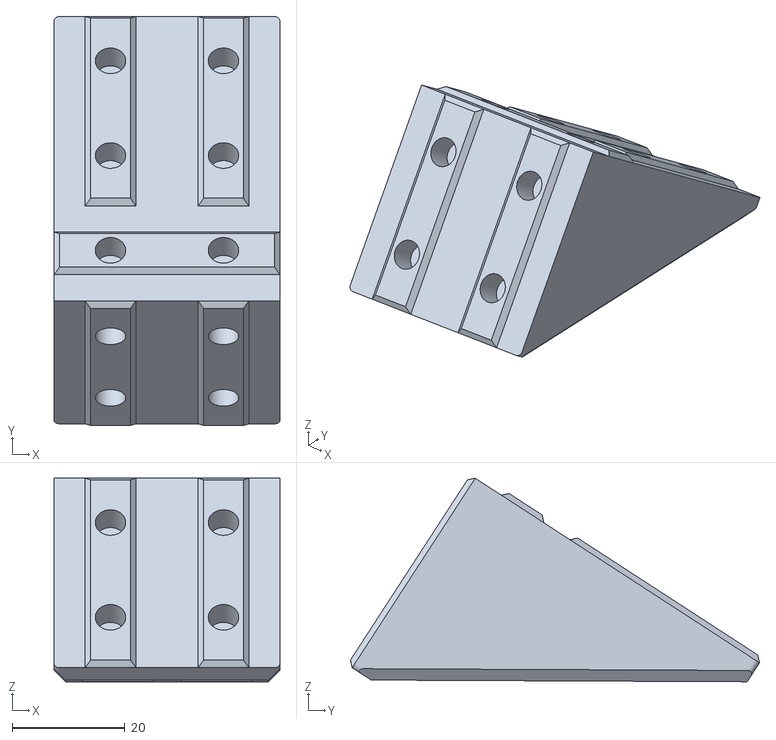
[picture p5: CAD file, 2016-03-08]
Completed_Builds/Carl_Feniak_Original_C-Bot/Parts/Rework Stls/Frame Brackets/Inside Corner 4x6 (x4) Optional.stl
40.0 x 72.4 x 36.0

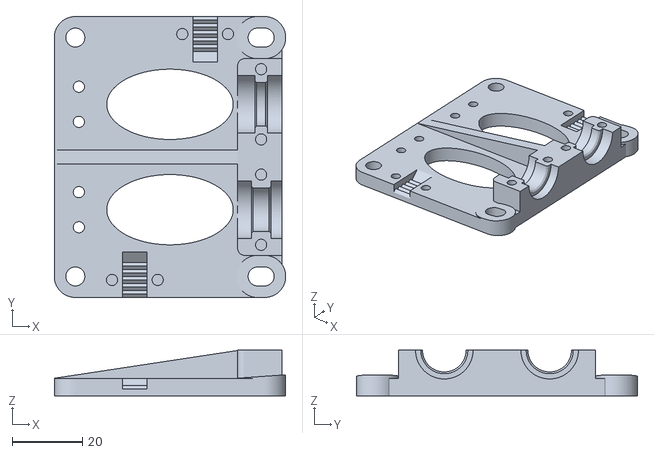
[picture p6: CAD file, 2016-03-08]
Completed_Builds/Carl_Feniak_Original_C-Bot/Parts/Rework Stls/Hot End & Filament Feed/Bowden Option/Dual Hotend/Bowden Dual Front Plate (x1).stl
65.9 x 80.0 x 13.0

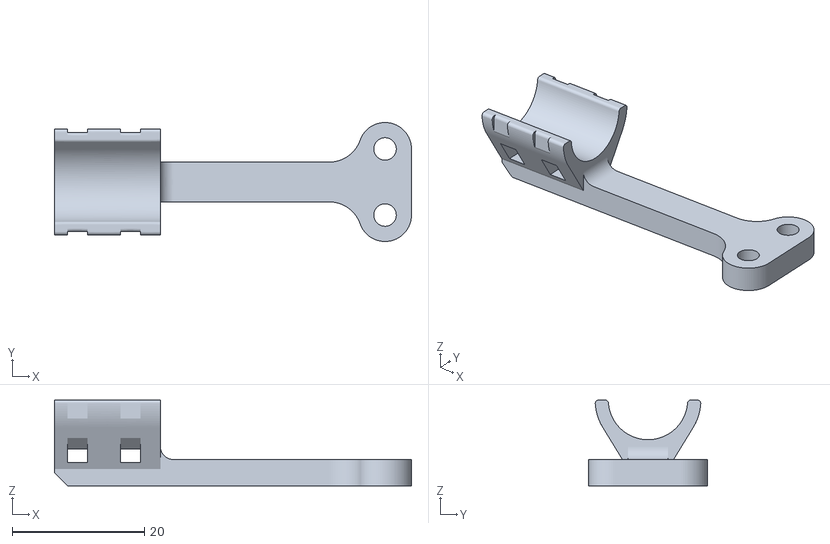
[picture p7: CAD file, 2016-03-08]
Completed_Builds/Carl_Feniak_Original_C-Bot/Parts/Rework Stls/Hot End & Filament Feed/Bowden Option/Single Hotend/Tube and Wiring Holder (x1).stl
54.0 x 18.0 x 13.0

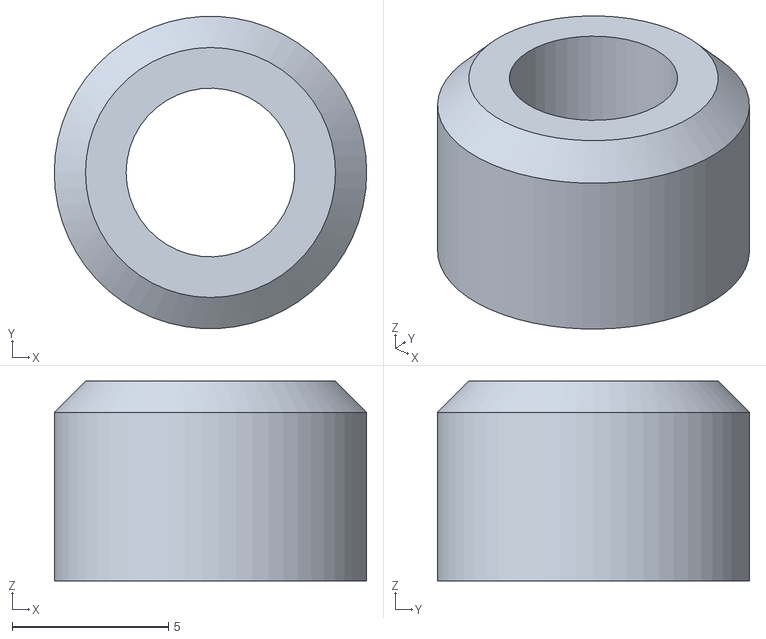
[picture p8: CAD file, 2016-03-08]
Completed_Builds/Carl_Feniak_Original_C-Bot/Parts/Rework Stls/Hot End & Filament Feed/Bowden Option/V-Wheel Spacer (x8).stl
10.0 x 9.99 x 6.40

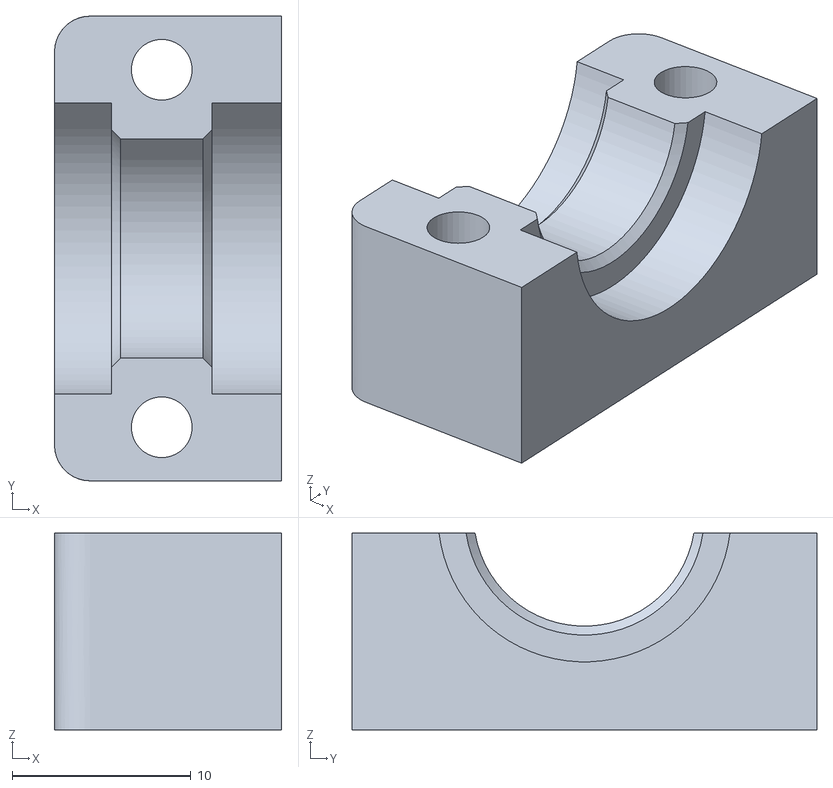
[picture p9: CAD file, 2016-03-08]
Completed_Builds/Carl_Feniak_Original_C-Bot/Parts/Rework Stls/Hot End & Filament Feed/Direct Feed Option/Groove Mount Clamp (x1).stl
12.7 x 26.0 x 11.0

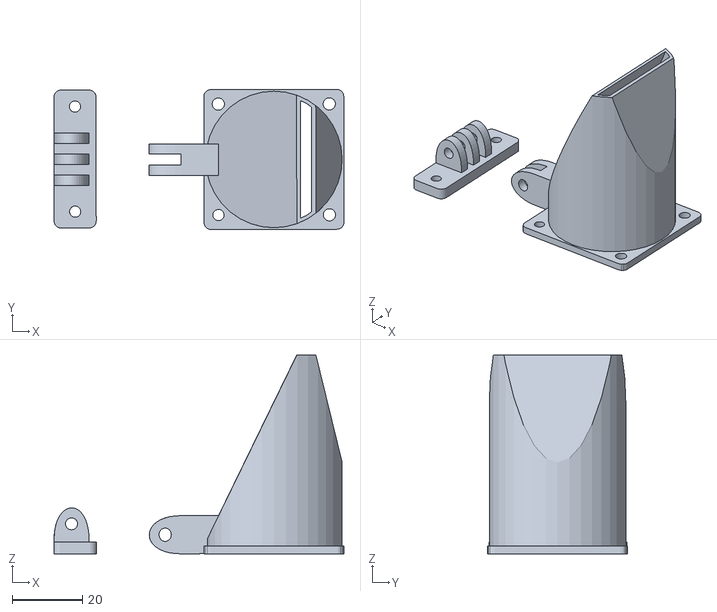
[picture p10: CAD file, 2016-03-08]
Completed_Builds/Carl_Feniak_Original_C-Bot/Parts/Rework Stls/Hot End & Filament Feed/Fan Duct by TruBlu832 (x1).stl
82.8 x 40.0 x 56.8

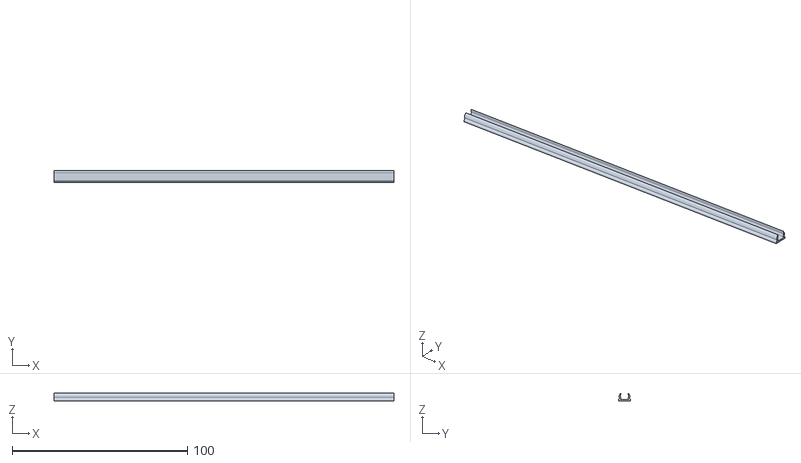
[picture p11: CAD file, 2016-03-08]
Completed_Builds/Carl_Feniak_Original_C-Bot/Parts/Rework Stls/Wiring Accessories (optional)/Wire Channel Long by Sheffdog.stl
194.0 x 6.97 x 4.51

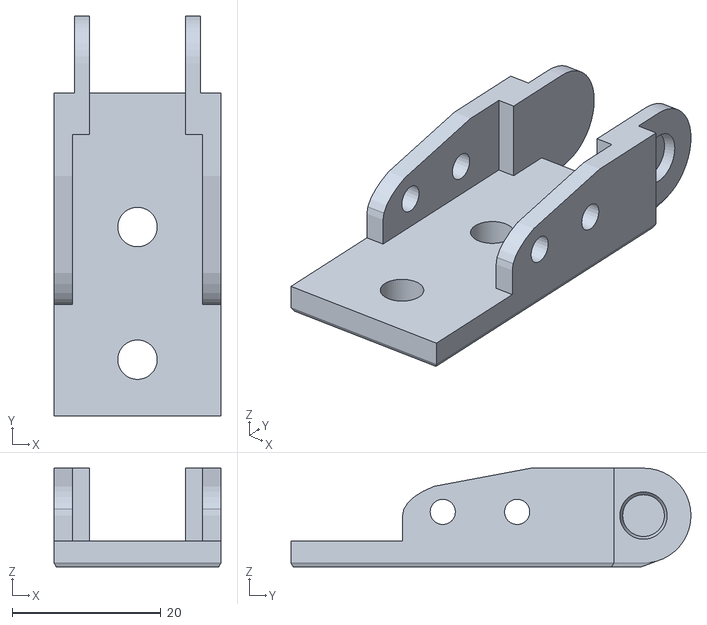
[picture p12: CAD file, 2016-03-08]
Completed_Builds/Carl_Feniak_Original_C-Bot/Parts/Rework Stls/Wiring Accessories (optional)/Wiring Accessories by Elmo Clarity/toplink.stl
22.4 x 53.8 x 13.3

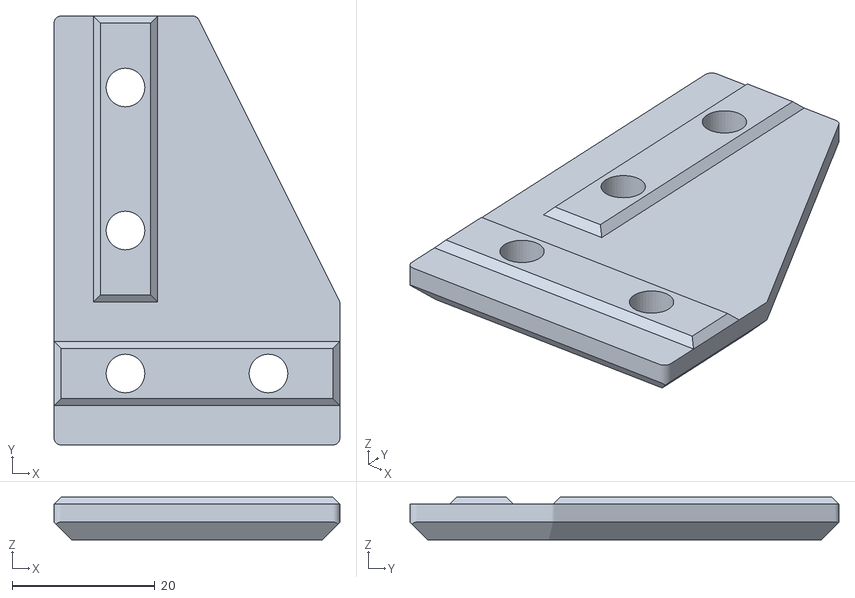
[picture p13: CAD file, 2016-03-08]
Completed_Builds/Carl_Feniak_Original_C-Bot/Parts/Rework Stls/Z Assembly/L Plate 2x3 (x2).stl
40.0 x 60.0 x 6.00

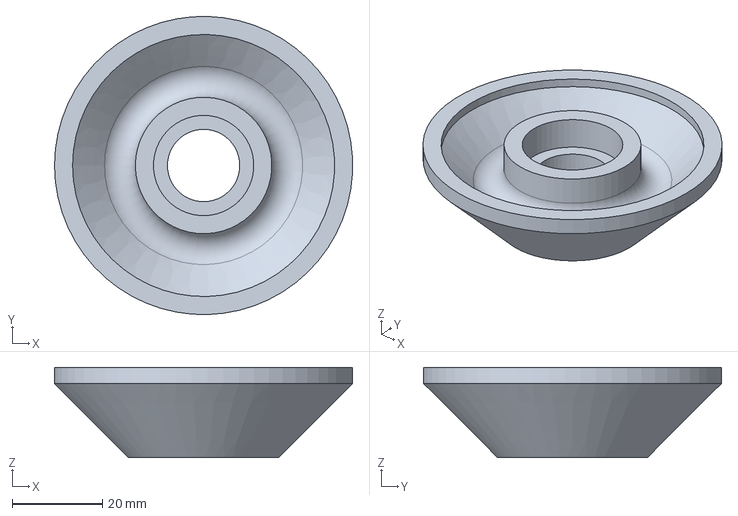
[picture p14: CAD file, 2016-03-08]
Completed_Builds/Carl_Feniak_Original_C-Bot/Parts/Original C-Bot/C-bot - STEP files_Rev2/Variable Spool Spindle 35-60mm.stp
66.0 x 66.0 x 20.0 mm

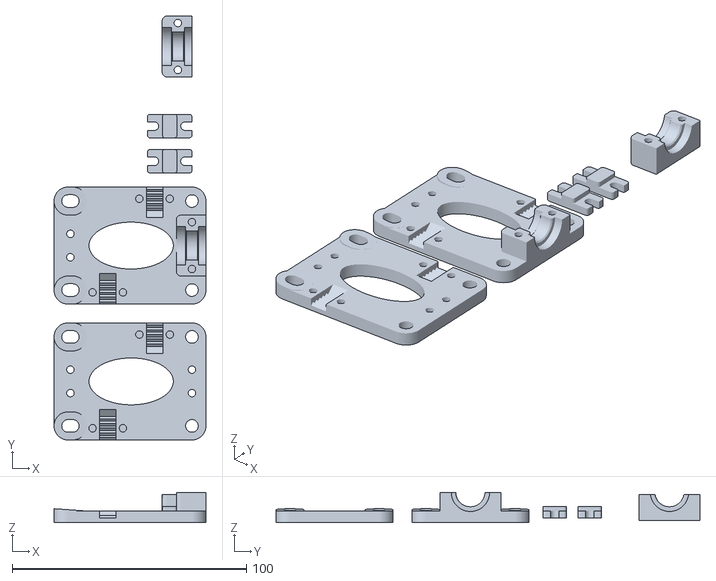
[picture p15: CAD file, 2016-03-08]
Completed_Builds/Carl_Feniak_Original_C-Bot/Parts/Original C-Bot/C-Bot STL Files/ExtruderCarriageSingle.stl
64.9 x 181.0 x 13.0

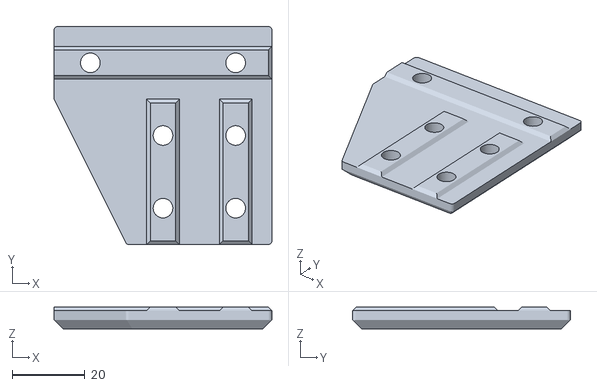
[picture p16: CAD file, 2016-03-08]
Completed_Builds/Carl_Feniak_Original_C-Bot/Parts/Rework Stls/Frame Brackets/L Plate 2x4 (x2).stl
60.0 x 60.0 x 6.00

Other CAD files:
Completed_Builds/Carl_Feniak_Original_C-Bot/Parts/Rework Stls/XY Assembly/V-Wheel Spacer (x16).stl
Completed_Builds/Carl_Feniak_Original_C-Bot/Parts/Rework Stls/Hot End & Filament Feed/Bowden Option/Bowden Filament Drive (x1).stl
Completed_Builds/Carl_Feniak_Original_C-Bot/Parts/Rework Stls/Hot End & Filament Feed/Bowden Option/Dual Hotend/Filament Spool Cone (x2).stl
Completed_Builds/Carl_Feniak_Original_C-Bot/Parts/Rework Stls/Hot End & Filament Feed/Bowden Option/Single Hotend/Bowden Single Front Plate (x1).stl
Completed_Builds/Carl_Feniak_Original_C-Bot/Parts/Original C-Bot/C-Bot STL Files/3x3 Corner.stl
Completed_Builds/Carl_Feniak_Original_C-Bot/Parts/Original C-Bot/C-Bot STL Files/90 Corner.stl
Completed_Builds/Carl_Feniak_Original_C-Bot/Parts/Original C-Bot/C-Bot STL Files/Bed.Supports.Alternate.by.Sheffdog.stl
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

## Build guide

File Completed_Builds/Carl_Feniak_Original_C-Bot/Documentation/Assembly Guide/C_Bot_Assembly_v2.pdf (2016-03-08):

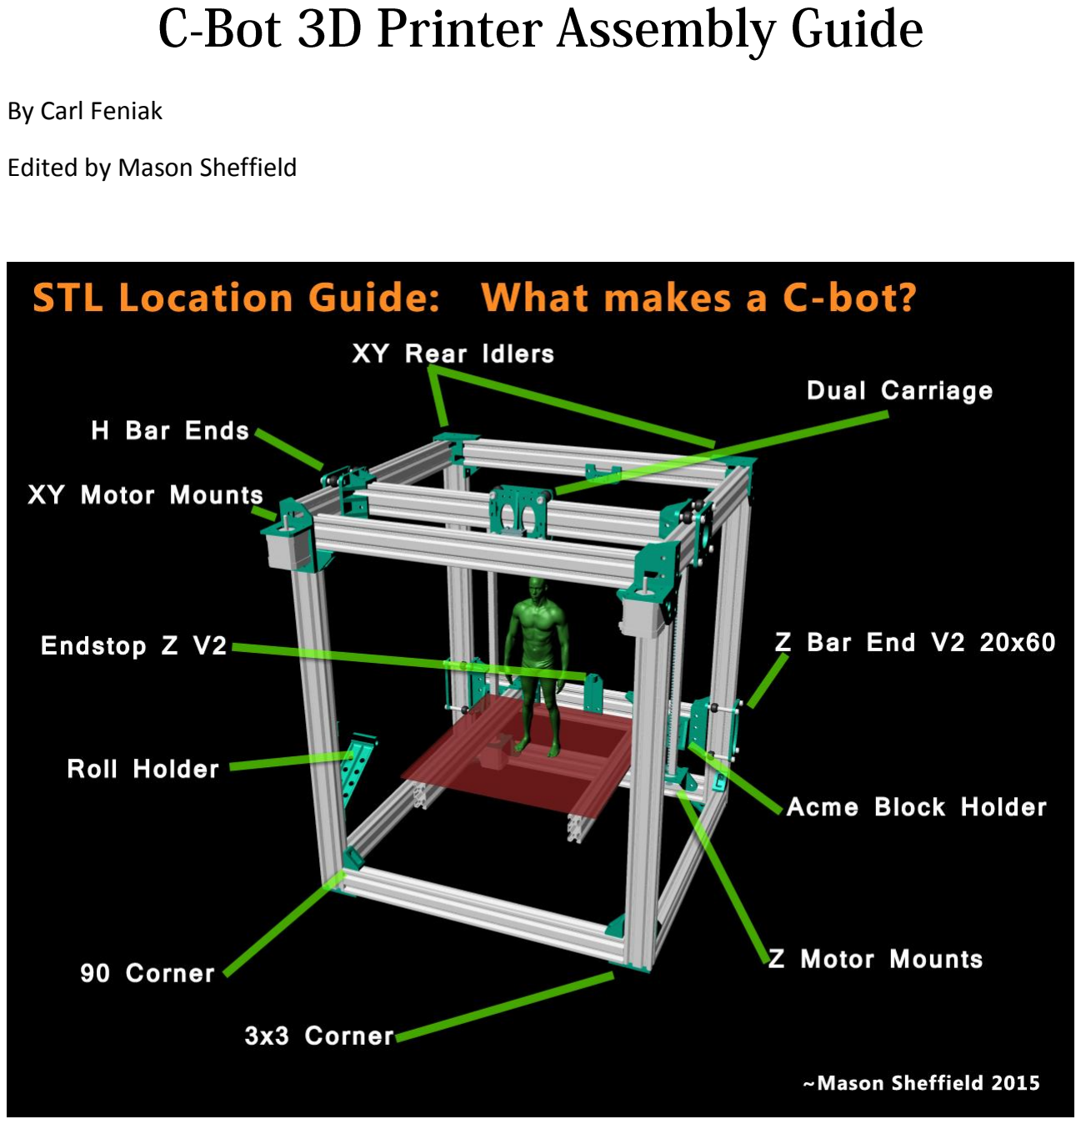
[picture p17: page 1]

By Carl Feniak

Edited by Mason Sheffield

## Pre assembly work:

1) Decide on a build volume
- For the XY plane, common sizes are 8x8”, 10x10”, 8x12”, 12x12”
- For the Z, a 300mm lead screw is typical, but not all this range will be usable
- I’d say up to 500mm is reasonable, but not a hard limit
2) Order parts
- Use the BOM and see sheet2 for a guide on extrusion length requirements
- Review the optional equipment
- Decided if you want to buy or 3D print certain components
- Try to reduced shipping costs by ordering from fewer suppliers
- Be aware that purchases from Ebay China may take 4-6 weeks to arrive and sometimes don’t arrive at all, but often items are 10-50% cheaper and have free shipping
- Choose a Hot End. I’d recommend all beginners to start with an official J-head. Rip-off hot ends are available on EBay <- avoid. This is NOT an item you want to cheap out on.
3) Decide on color and type of plastic for printed parts, order a 1kg spool
- I used PLA, but ABS would work very well
- Order multiple colors if you want to mix it up
- I always buy plastic in 3 packs to get free shipping
4) Print printed parts
- If you don’t have a printer your self
- See if there are other reprap owners in your area, check the reprap forums
- Join a maker/proto shop or hacker space
- Libraries in some areas are buying 3D printers
5) Cut extrusion
- I used a miter saw with a normal wood blade. I can’t advise this but aluminum cuts like butter.
- Safer options include:
- buying a metal blade for a miter saw/table saw,
- using a band saw,
- using a chop saw,
- and using a good miter block and fine toothed hacksaw (don’t use a plastic one meant for 2x4s!).

## Assembly:

### Load Idler pieces and CoreXY Ends with Flanged bearings Idlers:

1. Trim nut slots and insert regular M3 nuts.
2. Stack 2 F623ZZ flanged bearings with a M3 washer between them and load it into the assembly .

NOTE:
Try stacking the flanged bearings and an M3 washer on an M3 bolt and secure the stack with a thin strip of masking tape. Remove the m3 bolt and slide it into the corner piece. Slide a 25mm M3 bolt through the housing and bearings then carefully remove the piece of tape with Pliers or tweezers.
(Tip from Miertam)
3. Insert a 25mm M3 bolt through the assembly and lightly tighten.

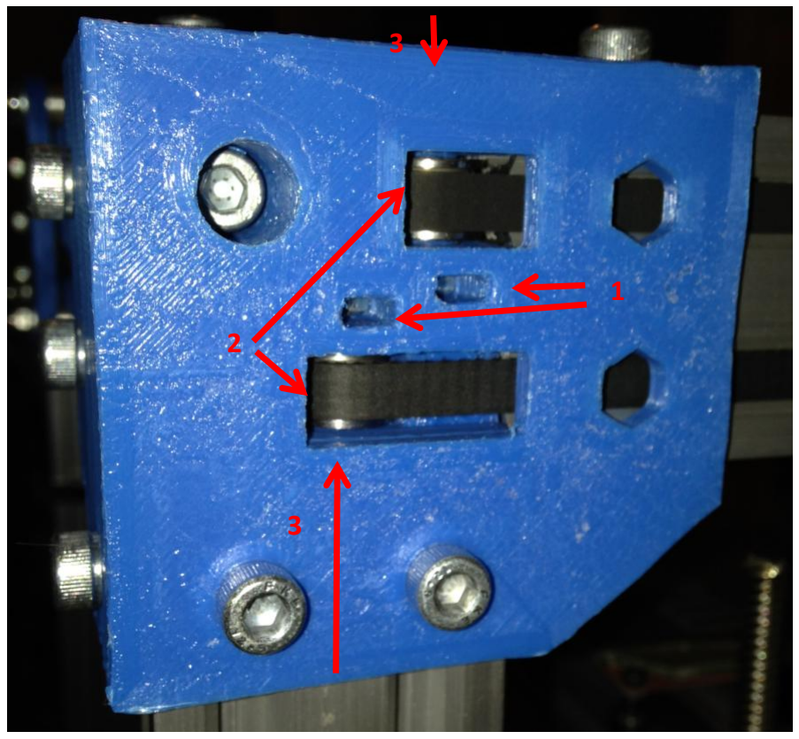
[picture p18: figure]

### - CoreXY Moving Rail Ends

1. Stack 2 F623ZZ flanged bearings with a M3 washer between them and load it into the assembly
2.Step 2: insert 25mm M3 bolts through assembly and lightly tighten. Use a M3 nyloc nut if available.

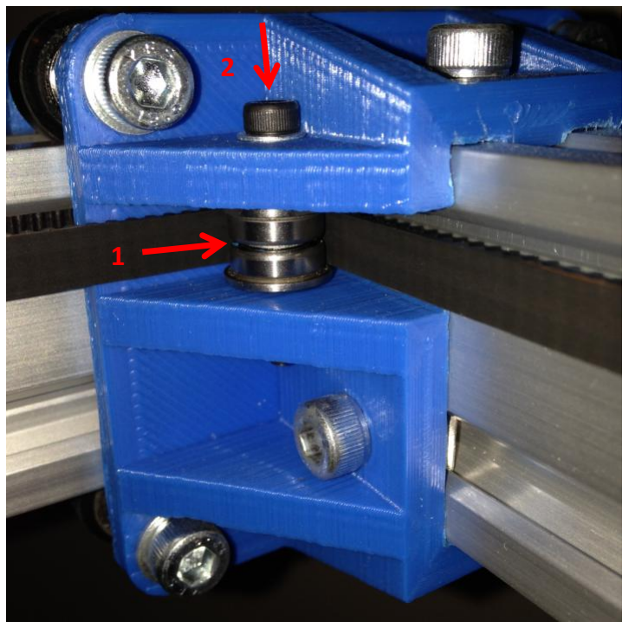
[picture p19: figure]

### Build Side frames

1. Drill and tap extrusion ends, this needs to be done for the two horizontal CoreXY rails (both ends) and the four vertical legs (one end each)

NOTE: Use an M5 tap if available. If you do not have access to a proper tap, drill to a depth of 4.5mm or 3/16” and slowly cut threads with an M5 bolt. Reverse out the screw frequently to clear the aluminum shavings or you will destroy your newly cut threads.

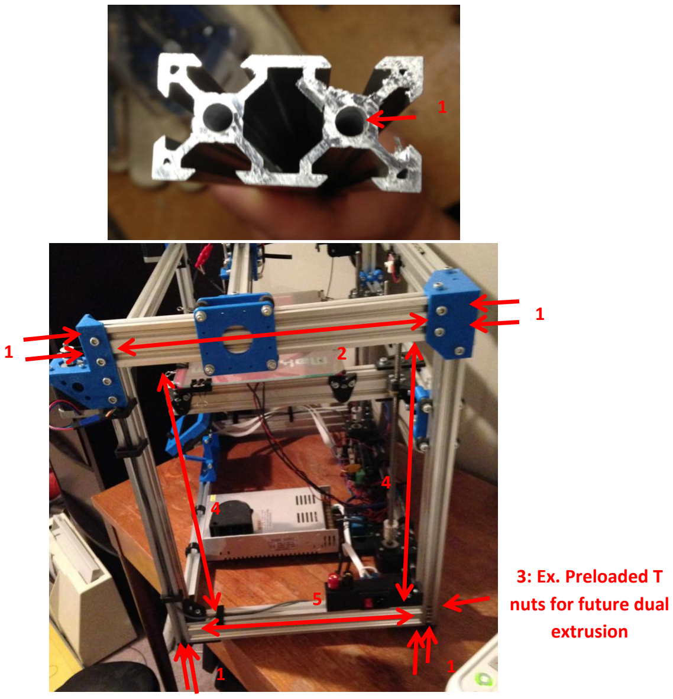
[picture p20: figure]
3: Ex. Preloaded T nuts for future dual extrusion

2. Assemble the CoreXY Idler brackets and Motor Mounts to the CoreXY rails. Use 10mm M5 bolts and T-nuts.

NOTE: Don’t over tighten or you may crack the plastic printed parts.

3. Preload the leg pieces and bottom horizontals with T-nuts for accessories as well as for the structural brackets.

NOTE: Remember things like the filament holder, electrical plug and switch holder, Z stop (planned future modification), extruder, and 90 deg. corner brackets for the horizontal pieces in the next step.

## - Attach legs to CoreXY rail

4. Attach L brackets to the bottom of the legs firmly and attach the 90 deg. corners loosely. Insert the bottom horizontal extrusion piece and tighten the corners.
5. If purchased, add a rubber foot to the bottom of the L bracket

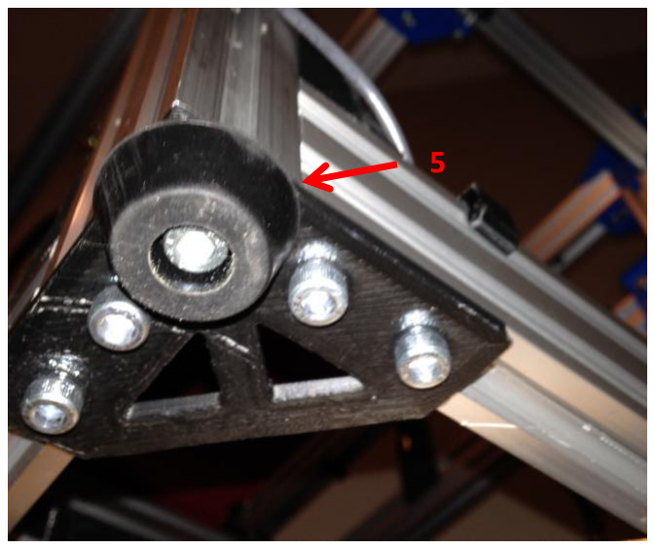
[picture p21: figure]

### - Square the frame

1. Check that all legs are the same length when measured within the top and bottom horizontals. If they are not equal adjust them to match the longest measurement by creating a slight gap.
2. Repeat this process with the horizontal measurements of the extrusion between the legs. These two steps will remove any chance of the frame being skewed into a trapezoidal shape.
3. Use a carpenter's square to verify the corners are straight. If the corners are not straight either the printed pieces are not square or a bracket is binding with the extrusion. To solve the latter, slightly loosen all brackets confining the non-square joint, square them up and retighten.

### - Connect Frame Ends to complete the cube

Connect the two frame ends assembled earlier with 4 horizontal extrusion pieces
You will need 4 equal pieces of extrusion and 6x 90 degree corner brackets (plus 10mm M5 bolts and T-nuts)

1. Preload the rear top bar and bottom rear bar with T-nuts for the brackets. Also preload T-nuts for the Z endstop, Y endstop, Z motor mounts, and other future accessories. Look at photos to ensure T-nuts are loaded in the correct slots.
2. Slide the bars onto the two assembled frame pieces and connect them. Tighten lightly.
3. Preload the front top and bottom bar with T-nuts for the brackets. Also preload T-nuts for the LCD mount if applicable.
4. Insert and tighten the two extrusion pieces.
5. Square the frame (similar to above) and firmly tighten all bolts.
6. Attach the two Z motor mounts onto the preloaded T-nuts.

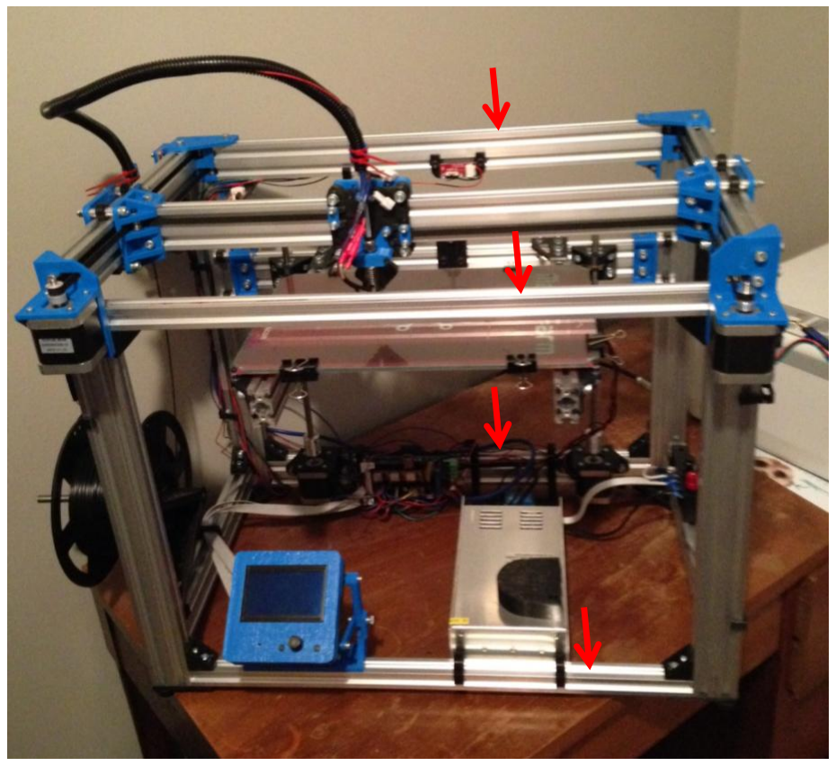
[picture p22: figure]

### - Assemble Z Frame (moving bed platform)

1. Arrange the pieces on a perfectly flat similar to the final assembly. Space the bars to the approximate with by using the heated bed as a guide. Load the necessary T-nuts into the top layer and install the two top T (or L) brackets.

2. Flip the assembly over and install the other two brackets.
3. Install the bed support mount (this can also wait until later as the extrusion ends are exposed for loading T-nuts).
4. Install the two Lead screw nut catches and the adjustable Z endstop bolt piece.
5. Assemble Z Frame linear Wheel pieces. Bolts should cut threads into the plastic bolt holes and be very firm. Important! --> insure there is an aluminum spacer between the two bearings in the delrin wheel.
6. Install half (front or back, not a pair) of the Z frame linear guide pieces. Keep one side loose and preload T-nuts for the others.
7. Place the partial frame into the main assembly and adjust the loose side so that the v wheel align with the V-slot extrusion. Attach the other two Z Frame linear guide pieces lightly. Run the assembly up and down the extrusion and then properly tighten all bolts.
8. Install the two Z motors with 8mm M3 bolts. Balance the position of the two Z motor mounts so they are equally spaced from the vertical legs used as a linear guide. Slide the Z frame down near the Z motor mounts and adjust the Z nut catches to align.
9. Attach the 5mm to 8mm couplings to the motor shafts. Insert the lead screws, clamp in place, then recheck the alignment of the motor shaft and Z nut catch at both the minimum and maximum travel positions. Adjust as necessary.

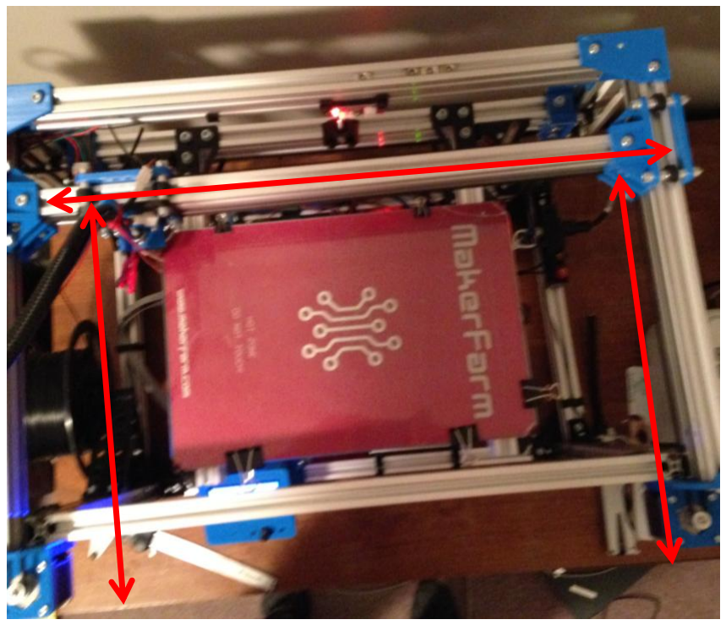
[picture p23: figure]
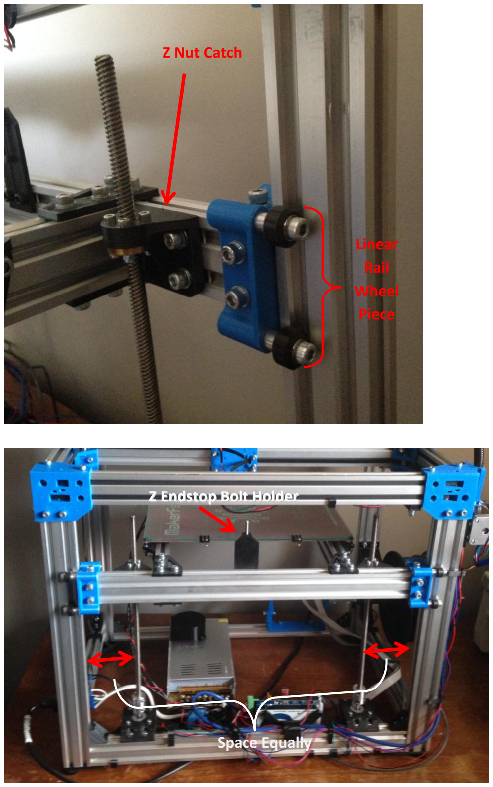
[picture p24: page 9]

Z Nut Catch

Linear
Rail
Wheel
Piece

Space Equally

Z Endstop Bolt Holder

### - Assemble CoreXY Bar

1. Load with T-nuts and attach end piece idlers to coreXY cross bar, leave one end loose for adjustment.
2. Connect the Idler back pieces to the idlers, but only with the top wheels.

This how the parts stack:
Bolt head - washer - plastic - spacer - wheel - spacer - plastic - washer - nut
3. Insert the assembly into the printer frame and adjust the loose idler on the extrusion piece to fit the wheels into the V-slot.
4. Insert the 4 bottom wheel bolts into the idler bottoms. Firmly clamp the top and bottom wheels together by hand and tighten the bottom bolt. Ensure all 8 bolts are tight.
5. Slide the bar to both ends to ensure it is square and then tighten the loose idler bolts.

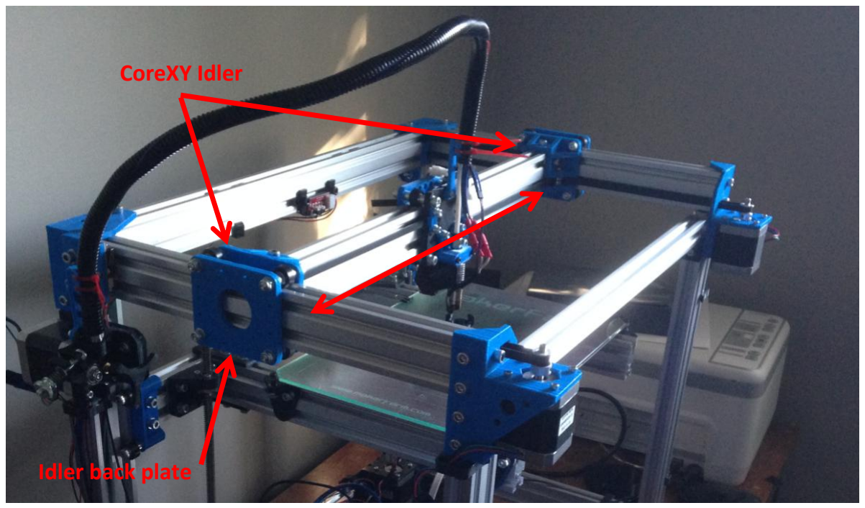
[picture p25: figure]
CoreXY Idler; Idler back plate

### - Assemble Hot end Carriage and install belt

1. Take the two carriage pieces and insert M3 nuts into the back of each side of the GT2 belt clamps (4 nuts in each plate), also insert 4 nuts corresponding to the hotend clamp locations in the front plate.
2. Connect the GT2 belt clamps and the hotend clamp to help retain the M3 nuts. Use 10mm M3 bolts for all except the bottom two hotend clamp bolts. Use 25mm bolts for those.
3. Connect the two plates at the bottom with two wheel assemblies, place in one the CoreXY bar and, in the same manner of the CoreXY bar idlers, insert the other two wheel assemblies and tighten.
4. Install the two CoreXY motors with 8mm M3 bolts and attach the 16tooth GT2 pulleys to their shafts.
5. Run the GT2 belt through the extrusions, around the idlers and pulleys, then to the hotend carriage. Place the belt under the clamps and tighten the two front clamps. Don’t over tighten or the plastic will split on the layers or the bolt ends will touch the aluminum extrusion.
6. Push the entire bar to the front of the printer to insure that it is square, pull the belt end on the back plate firmly through the clamping spot and tighten. Do the same for the other belt. The assembly should remain square. If not, then one belt might be notably tighter than the other.

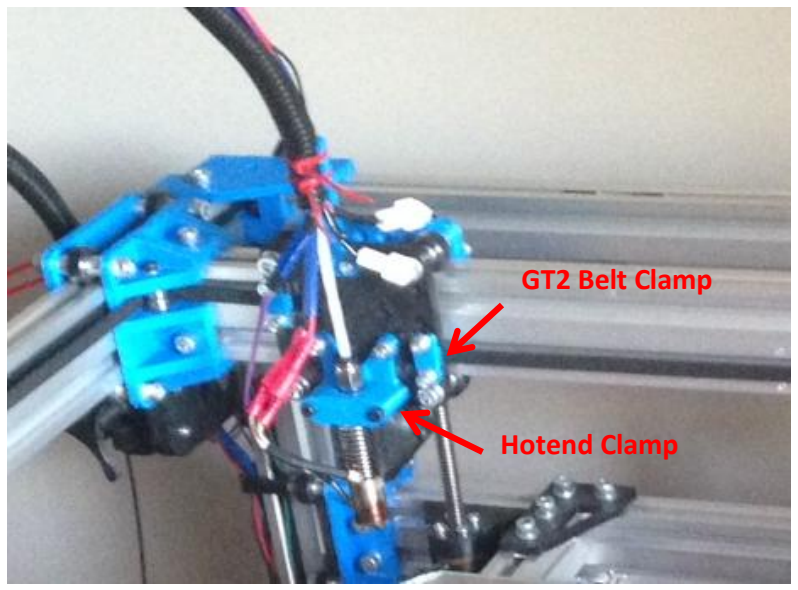
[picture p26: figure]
Hotend Clamp; GT2 Belt Clamp

### - Wiring, Programming, and Tuning

I will not provide details for these subjects since there are many resources available online to help with these steps.

A few notes and words of advice below

- I used a ramps 1.4 setup with Marlin installed
- Used pronterface as an interface before I started printing from SD cards, it also helps with calibrations.
- I am using slic3r to convert STL to G-code files that are ready to print.
- Oil the lead screws before attempting to tune your stepper drivers.
- If you have question then send me a message.
- The switch lever on the Y end-stop needs to be bent like the photo below so that it can home while in the home position.
If you don’t do this, the metal arm will snag and break. A lesson I learned the hard way.

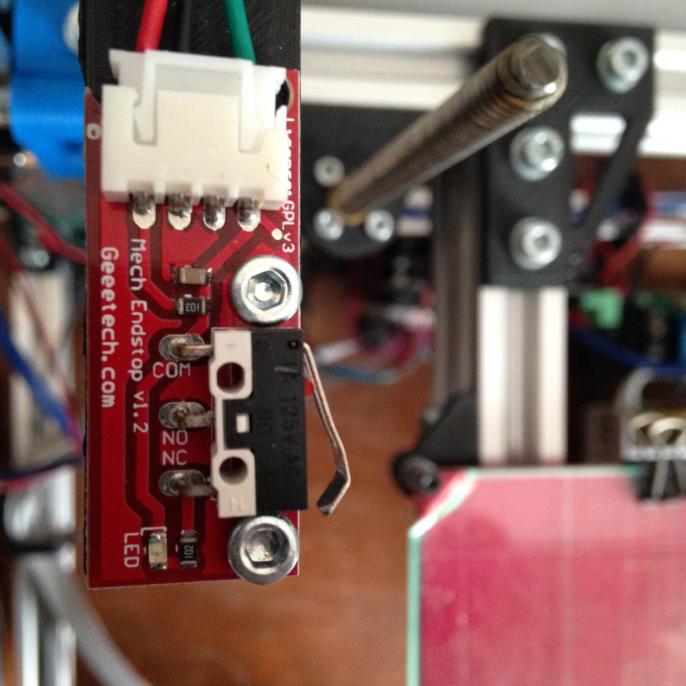
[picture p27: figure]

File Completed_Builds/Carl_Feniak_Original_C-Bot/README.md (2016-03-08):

# Author:

Carl Feniak

# Created

2015(?)

# some other info

this is the file where you tell everyone about your build... i guess.

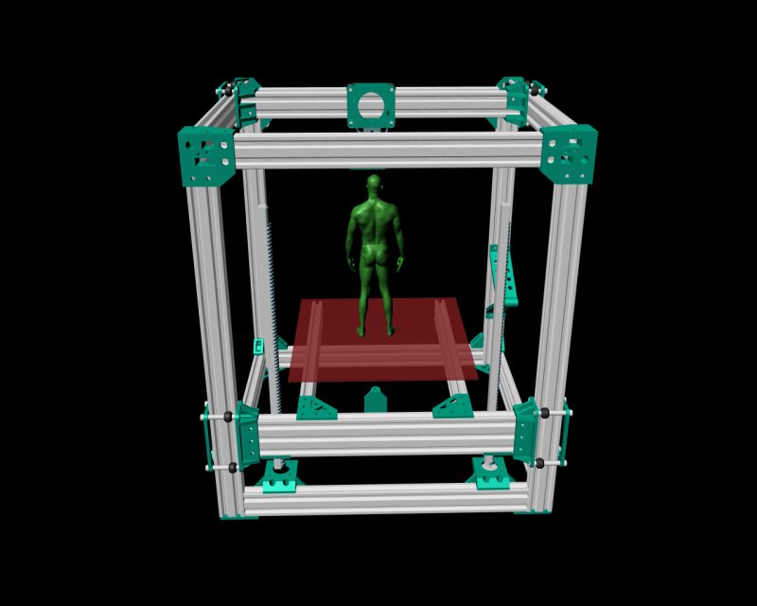
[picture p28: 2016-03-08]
Completed_Builds/Carl_Feniak_Original_C-Bot/Documentation/Assembly Guide/C_botBack.jpg

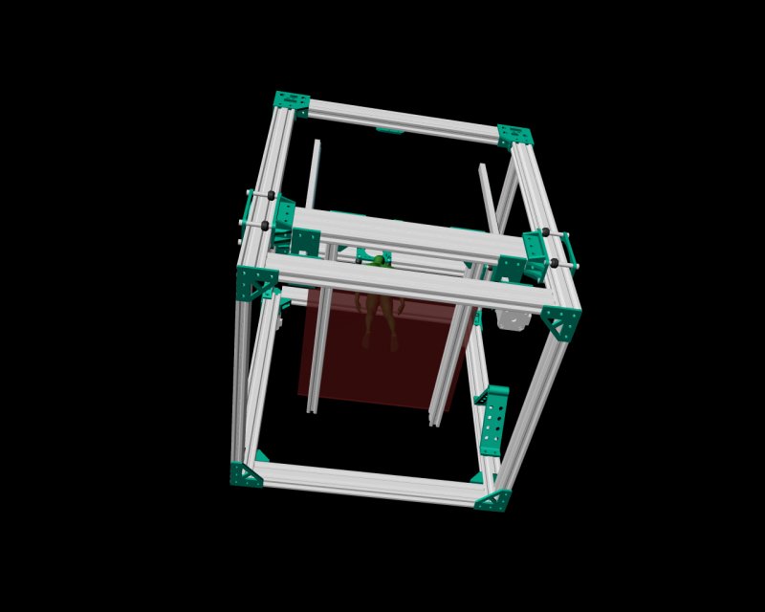
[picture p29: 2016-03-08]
Completed_Builds/Carl_Feniak_Original_C-Bot/Documentation/Assembly Guide/C_botBottom.jpg

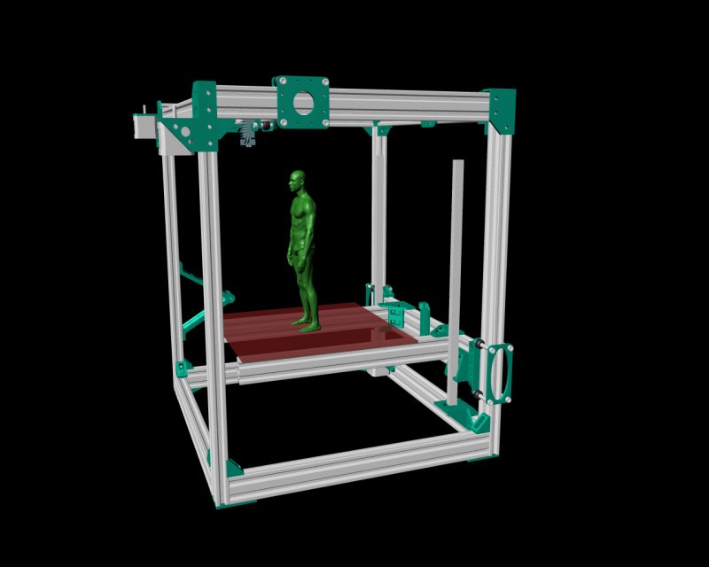
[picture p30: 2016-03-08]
Completed_Builds/Carl_Feniak_Original_C-Bot/Documentation/Assembly Guide/C_botLeft.jpg

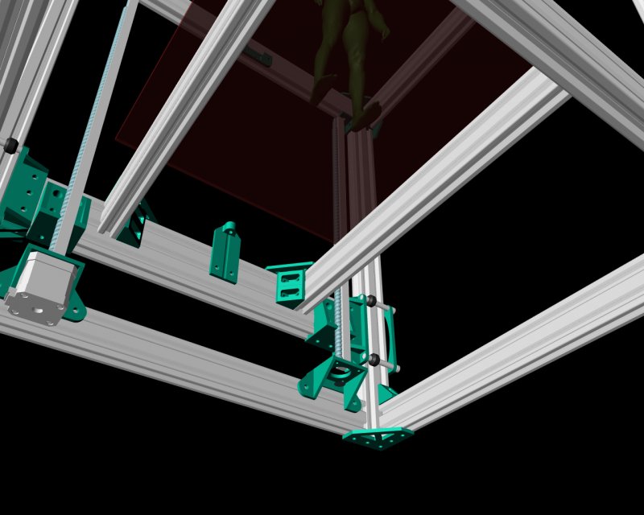
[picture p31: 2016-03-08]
Completed_Builds/Carl_Feniak_Original_C-Bot/Documentation/Assembly Guide/zPlatformDetail.jpg

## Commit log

2016-03-08 roughly added Carls c-bot as an example
    [3x3 Corner.stl, 90 Corner.stl, AcmeBlockHolder.stl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]
2016-03-08 added magentabot, updated readme
    [3x3 Corner.stl, 90 Corner.stl, AcmeBlockHolder.stl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]
2016-03-08 renamed and moved folders
    [3x3 Corner.stl, 90 Corner.stl, AcmeBlockHolder.stl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]
2016-03-08 removed c-bot prefix from carls files
    [Belt Clamp (x4).stl, Bowden Carriage Rear Plate (x1).stl, Bowden Dual Front Plate (x1).stl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]
